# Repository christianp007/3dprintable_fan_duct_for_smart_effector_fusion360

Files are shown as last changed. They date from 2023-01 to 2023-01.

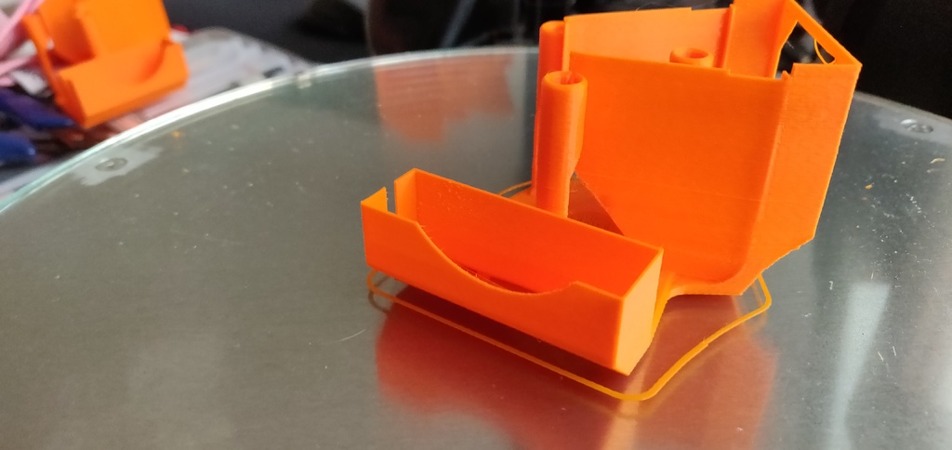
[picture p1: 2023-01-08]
images/1.jpg

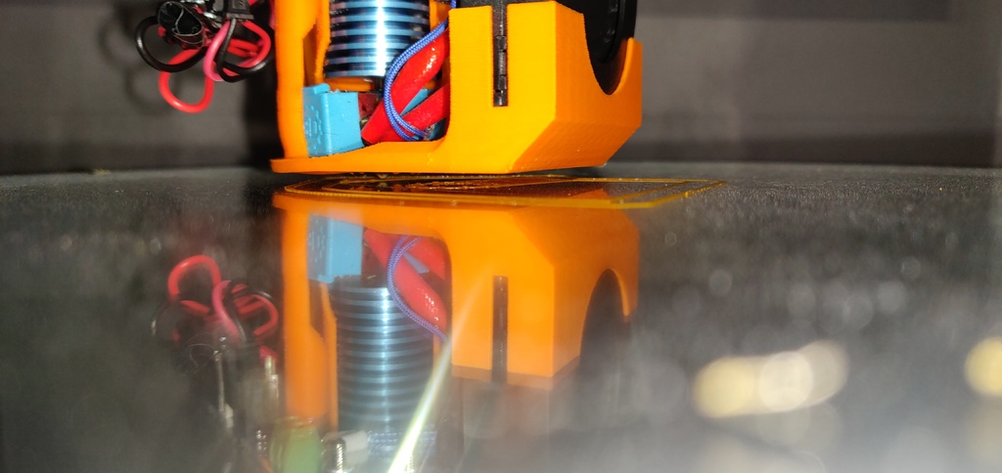
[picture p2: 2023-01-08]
images/3.jpg

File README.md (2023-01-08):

# 3dprintable_fan_duct_for_smart_effector_fusion360
 A 3d printable fan duct for the delta smart effector designed in Fusion360

I wasn't happy with the cooling performance of the conventional fan duct on my Smart Effector.<br>
Especially on small parts the air wasn't coming close enough th to nozzle tip to effectivly cool the part, additionally the cooling effect was different on all sides of the model.

Design goals:<br>
airflow as close as possible at the nozzle<br>
equal cooling on all sides<br>
simple mounting, if possible single part design<br>
include 40mm hotend fan adapter for silent operation<br>
It's a single part print without support which attaches magnetically to the screws/nuts on the extra mounting holes on the smart effecor. So these can still be used for mounting i.e. a zesty nimble (like on my printer) and the assembly can be taken off within seconds.<br>
For part cooling i'm using a blower fan because high pressure is needed which axial fans do lack, i used a 50mm one but 40mm might work, too (couldn't find one locally which was specified for 24V)<br>

This totally CAN be printed using PLA, but make sure to use a silicon sock and enable the part cooling fan at all times or it will eventually melt away :-D<br>
For PLA i recommend to anneal it. This can be done while mounted, just increase the temperature slowly from 45 to 120 degrees over about an hour with a very low setting of the part cooling fan and then keep it there for another hour.<br>
I successfully printed Nylon at 260 degrees using this printed in PLA.<br>
However PLA will not withstand the temperature forever, so be prepared to replace it or use higher temperature matierials like ABS or Nylon.<br>
I already printed one in Nylon but haven't tested it yet.<br>

There is about 1mm of clearance left between the bottom of the fan duct and the printed part.<br>
However over time the small "finger" slowly droop down due to the heat radiated by the nozzle. Maybe it would be better to have all the "fingers" connected (?)<br>
I used it for dozends of hours before I had to replace it as the air channels slowly closed due to the PLA melting.<br>

It's a work in progress, and I'm happy to get your feedback :-)

Weight ist only about 13g using PLA.<br>
I designed it for printing with my 0.25mm nozzle, so wall thickness is usually 0.6mm.<br>
Should be printable with a 0.4mm nozzle as single walls however.<br>
Layer height: 0.15mm<br>
I added a sacrificial bridge where the nozzle will go.<br>

Magnets used are: dia 5mm, length 8mm but you can use smaller ones and glue them in.<br>
Blower: dia 50mm, width 15mm<br>
Hotend fan: 40x10mm

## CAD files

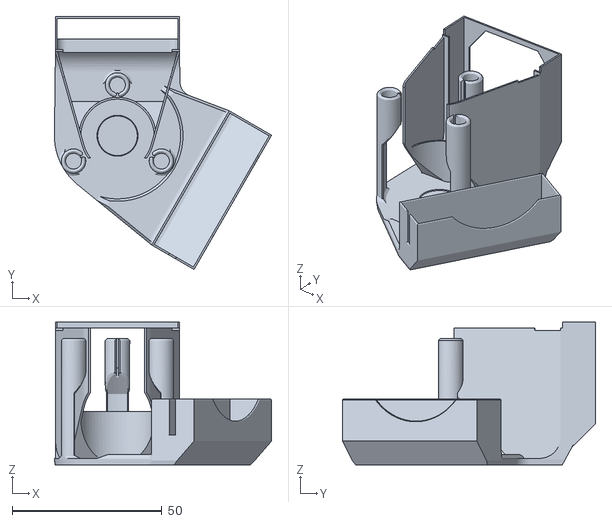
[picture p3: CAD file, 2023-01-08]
Smart Effector Fan Duct Rev.C v53.stl
72.6 x 84.6 x 47.8

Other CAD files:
Smart Effector Fan Duct Rev.C v53.f3d
